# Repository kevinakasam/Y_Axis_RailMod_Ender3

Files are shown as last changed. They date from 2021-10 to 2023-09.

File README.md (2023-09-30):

# Y Axis Linear Rail Mod for the Ender3
Upgrade your Ender 3 to a single or dual rail Y Axis. Ender 3 Pro and Ender 3 V2 will be supported later.

1: Single Rail        |  2: Dual Rail
:-------------------------:|:-------------------------:
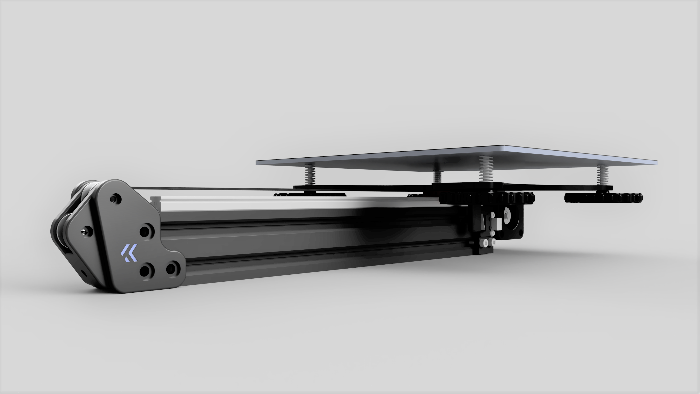
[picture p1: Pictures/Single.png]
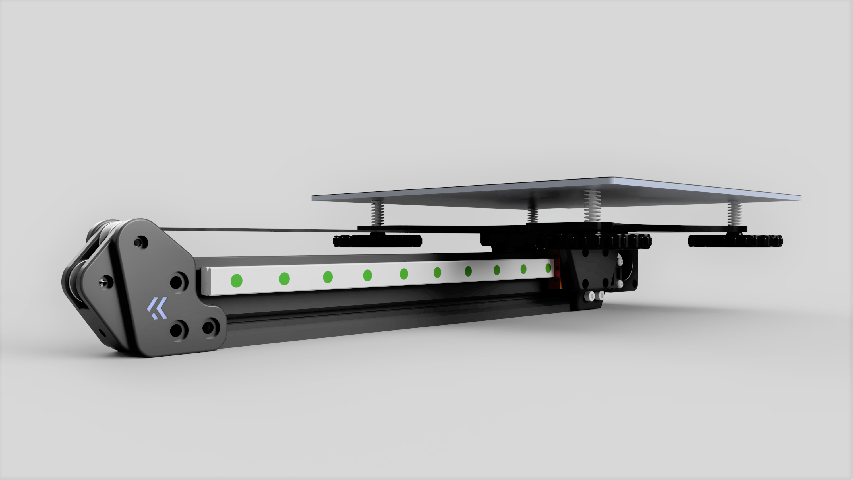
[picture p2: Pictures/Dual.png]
  |  
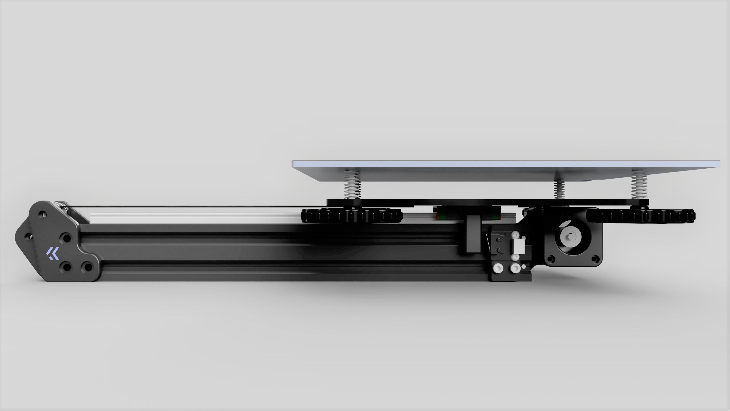
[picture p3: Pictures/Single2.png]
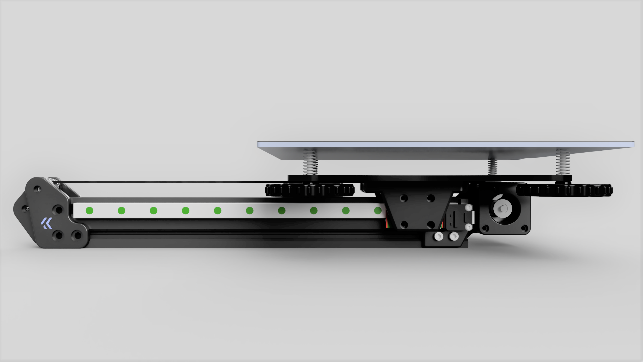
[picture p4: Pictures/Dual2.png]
  |  
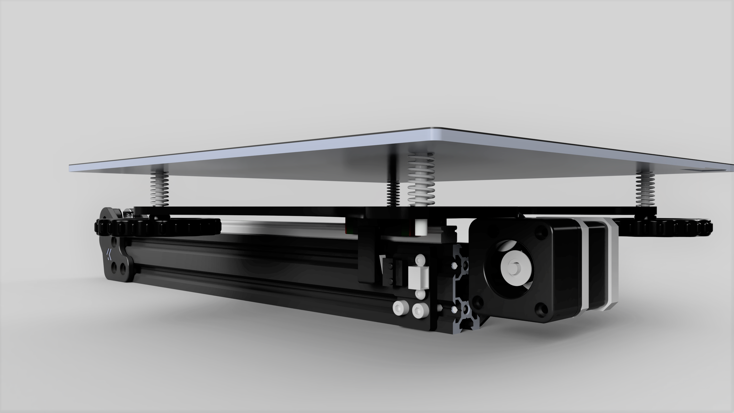
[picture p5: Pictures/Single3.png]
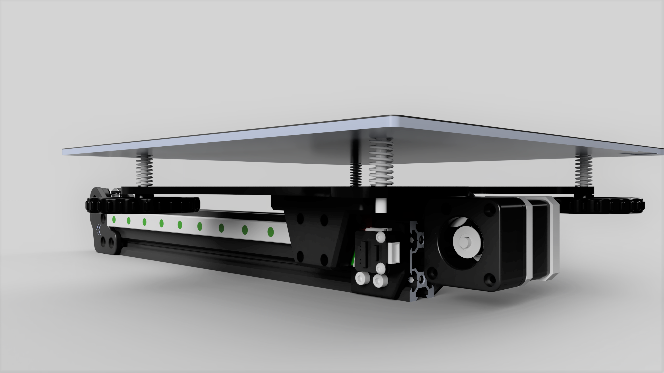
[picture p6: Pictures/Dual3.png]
  |  

## Why?
Just for fun, the Ender 3 prints very well even with the V Wheehls. The goal of this mod is not to reuse as many parts as possible from the Ender 3, but to create a very good working rail conversion for the Y axis. It includes parallel belt paths and a belt tensioner. All belts are guided by 20T idlers. The original metal motor plate of the Y-axis is reused to make everything as stable as possible.

## What?
There are two versions of the mod: Single Rail and Dual Rail. Both are compatible with each other, which means if you want to switch from single to dual (or the other way around), you don't have to reprint all the parts.

## How?
### Single Rail:
To attach the Single Rail to the Y Plate you need to drill 4 holes in it. I designed a drill guide that makes drilling very easy, even with a cordless screwdriver. Little pro tip: If the holes should be misaligned even with the drill guide, one, maximum two holes can be drilled out to 4mm. the other two holes align the Y Plate, and the two 4mm holes are used for additional attachment. ~~The single rail version uses an arm to reach the endstop. The endstop itself stays in the stock position with the stock braket.~~ Just use a screw for this, take a look at the BOM.
### Dual Rail:
The Dual Rail version does not need to be drilled. Instead, a printed adapter attaches the two rails to the Y Plate. A total of 6 screws fix the Y Plate to the printed part. With the dual rail setup it is very important that both rails are parallel, otherwise it is very difficult to move the Y axis. See my video explaining how to align the rails (video coming soon). The dual rail version needs a new endstop braket.

## How to print?
All parts are already aligned in the optimal position for printing. Support is not needed. Use at least PETG or better ABS (+) to print the parts. My settings: 5 walls/top/bottom, 55% infill.

## What do I need to build it?
```
## Common ##
4* M3x25
2* M3x16
1* M3x8 
3* M3 Hexnut
1* min. M5x12 (depends how you deep you tap the profile)
6* M5x8 (to mount the tensioner)
6* M5 tnut (to mount the tensioner)
1* 20T-5 Pulley (replaces stock pulley)
3* 20T-3 Idler (2 in the front, 1 in the back)
2 Meter GT2 6mm Belt (Glassfiber reinforced (no steel!))
M5 tapping tool (to tap the lower profile hole on the front for the tensioner)

## Dual ##
2* MGN-12H-300mm
32* M3x8 (8 to mount Printed Block to rail; 12 per rail for all holes (use min 6 per rail!))
24* M3 tnut (see one above)
4* M5x12
4* M5 locknut

## Single ##
4* M3x6
12* M3x8 (12 for all holes on the rail(use min 6 per rail!))
```
<br>

### ❤️ Support my work

All my work is 100% Open-Source and free for everyone to use. But designing and developing all these mods takes a lot of time and effort, so if you appreciate my work and would like to support it and also help cover the costs of gettings the mods perfect, you can use one of the following links. Thanks a lot 🤍

<a href="https://www.buymeacoffee.com/kevinakasam" target="_blank">Buy Me A Coffee</a>


<br>
12* M3 tnut (see one above)
1* M5x35 (Use this as new endstop trigger, you can use an M3/M4 as well, than add a washer to the head)
1* M5 locknut (or M3/M4 if you went for an M3/M4 for the trigger one above)
3mm drill bit (to drill the holes in the plate for the MGN) ```

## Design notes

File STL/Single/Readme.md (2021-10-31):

All files that belong to the single rail version.

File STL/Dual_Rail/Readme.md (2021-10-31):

All files that belong to the dual rail version.

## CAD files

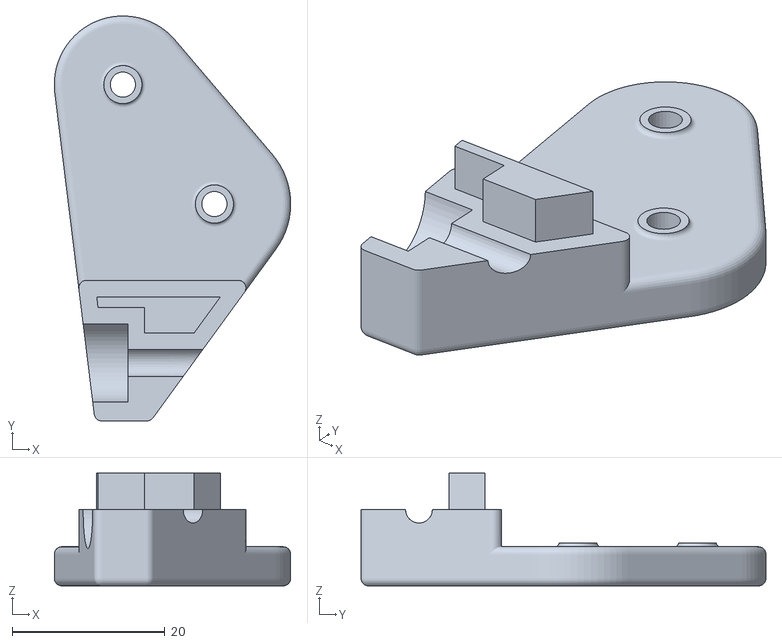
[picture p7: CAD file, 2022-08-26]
STL/Common/1_tensioner_arm_B.stl
31.0 x 53.1 x 14.8

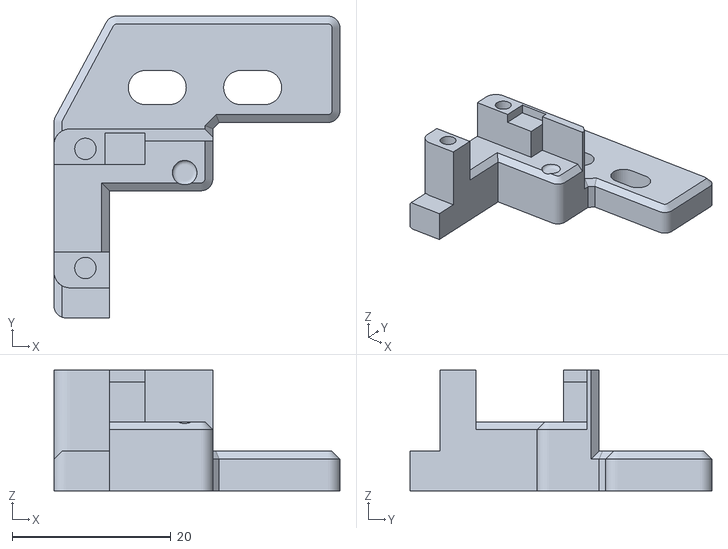
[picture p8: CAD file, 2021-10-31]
STL/Dual_Rail/1_dual_rail_limitswitch_braket.stl
36.0 x 38.0 x 15.2

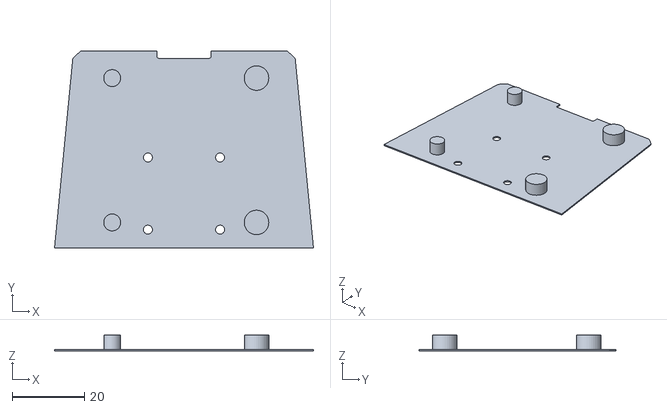
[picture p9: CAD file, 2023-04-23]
STL/Single/1_single_rail_drill_guide.stl
71.8 x 54.6 x 4.40

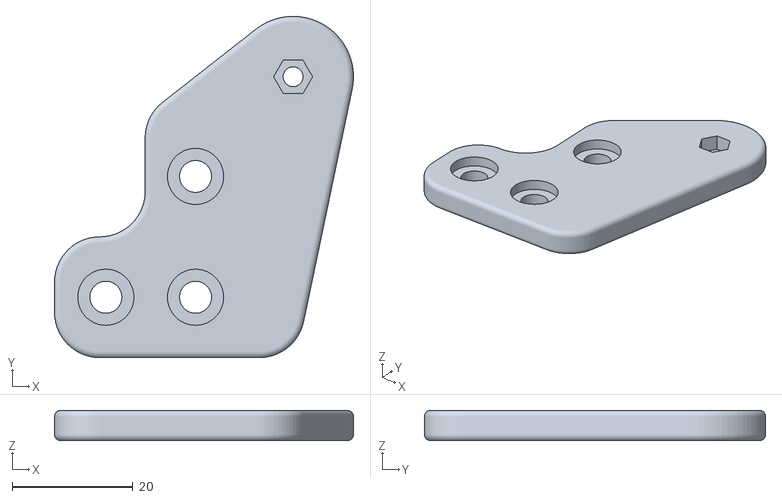
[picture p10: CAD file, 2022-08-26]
STL/Common/1_tensioner_mount_A.stl
49.5 x 56.5 x 5.00

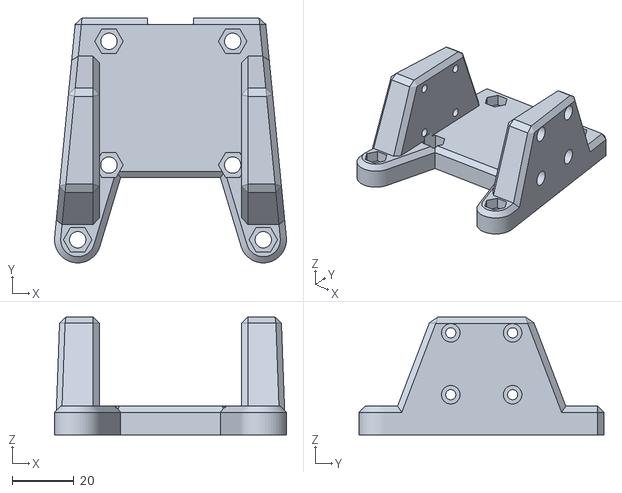
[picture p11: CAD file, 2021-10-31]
STL/Dual_Rail/1_dual_rail_nodrill.stl
75.0 x 79.1 x 38.1

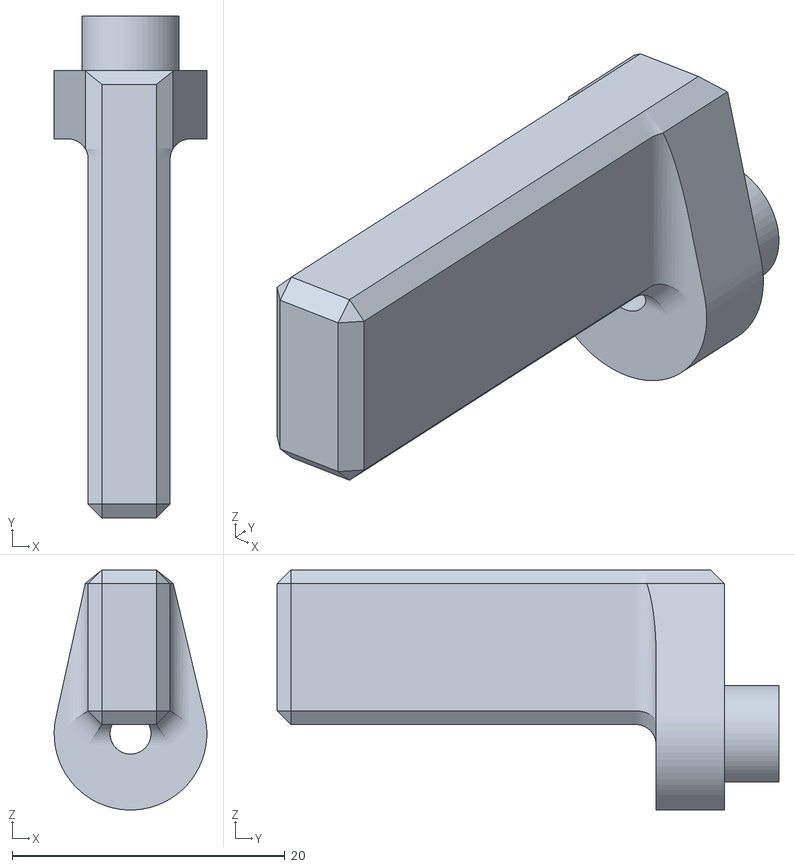
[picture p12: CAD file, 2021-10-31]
STL/Single/1_single_rail_limit_switch_arm.stl
11.2 x 36.8 x 17.6

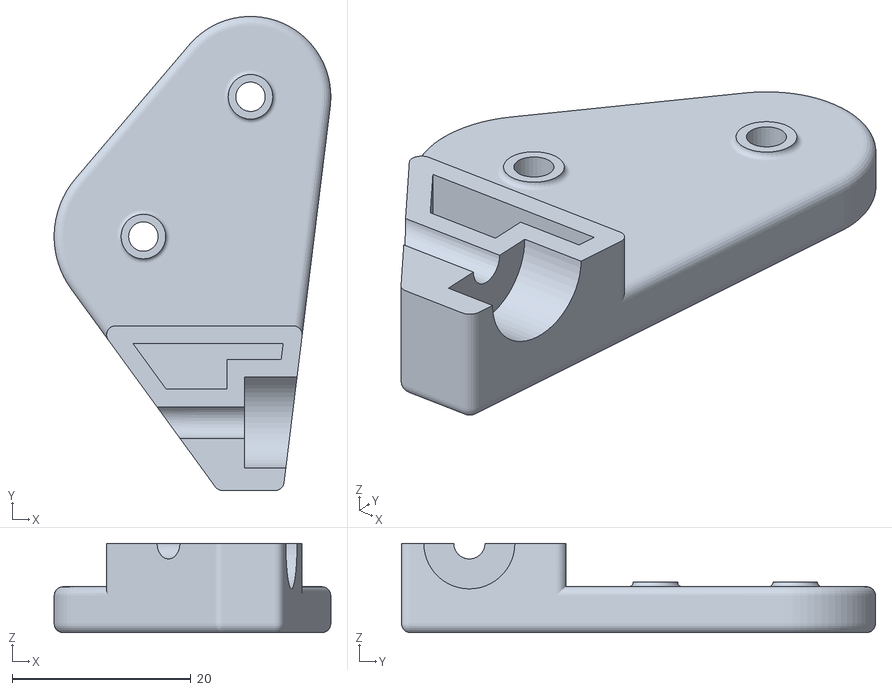
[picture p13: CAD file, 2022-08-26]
STL/Common/1_tensioner_arm_A.stl
31.0 x 53.1 x 10.0

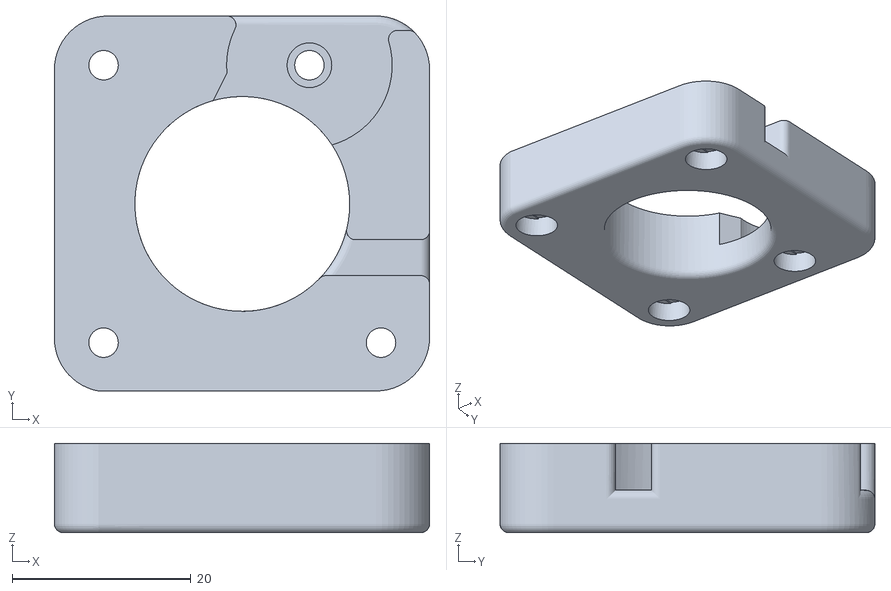
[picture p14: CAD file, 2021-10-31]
STL/Common/1_motor_housing_front.stl
41.9 x 41.9 x 10.0

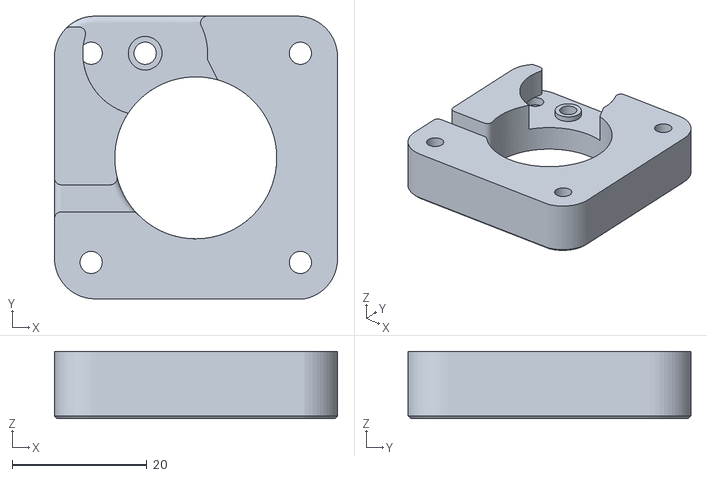
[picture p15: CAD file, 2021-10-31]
STL/Common/1_motor_housing_back.stl
41.9 x 41.9 x 10.0

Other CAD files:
STL/Common/1_tensioner_mount_B_logo.stl
STL/Common/1_tensioner_mount_A_logo.stl
STL/Common/1_tensioner_mount_B.stl

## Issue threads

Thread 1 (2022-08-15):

Any chance for a Ender 3v2 version?

lyonmaster, 2022-08-15:
The Ender 3v2 has a 4040 center rail, so does my Ender 3 Max.  I could upgrade two machines with this.  I already have my E3V2 apart with your dual belt kit and KlackEnder-probe installed, just waiting on a couple of parts to finish it off.  I would love to install the linear rail on this printer.  Thanks for the wonderful mods.  I'd try to modify the .step file myself, but i only know how to use Sketchup for my wood working.

kevinakasam, 2022-08-15:
Thanks for the kind feedback! I got this request quite often so far but I really have to time to work on this as well, maybe once my website is online and all the instructions are done. Feel free to join my discord and ping me from time to time, maybe I will find a minute to do this :)

tekgamerpt, 2023-01-18:
Wainting for a Ender 3 V2 version aswell, already have the belt conversion and its awesome

DJDaved5653, 2023-01-21:
I have just designed one if you want it just get me on discord DJDaved#5653

tekgamerpt, 2023-01-21:
Thanks!

StackingDeezLayers, 2023-02-26:
I am very interested as well. I hope this happens eventually

dwzg, 2023-03-22:
Just here to support a version for the Ender 3 Pro/V2. Would be awesome if you can find the time for this.

DARKFiB3R, 2023-03-26:
Also Interested :)

DJDaved5653, 2023-09-12:
Hey guys here is a zip that has the stl for the duel rail and single rail for the ender 3 that has 4040 extrusion instead of 2020.
[Ender 3v2 4040 extrusion linear rail mounts.zip](https://github.com/kevinakasam/Y_Axis_RailMod_Ender3/files/12581375/Ender.3v2.4040.extrusion.linear.rail.mounts.zip)

Have fun!

Catniped, 2024-02-02:
hey @DJDaved5653, could you please provide some pictures or instructions of how this is supposed be used? i cant figure out how its supposed to work

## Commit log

2022-08-26 Little Update
    [1_tensioner_arm.stl, 1_tensioner_arm_A.stl, 1_tensioner_arm_B.stl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]
2022-10-05 Added BOM
2023-04-23 Fixed missing holes
    [1_single_rail_drill_guide.stl]
